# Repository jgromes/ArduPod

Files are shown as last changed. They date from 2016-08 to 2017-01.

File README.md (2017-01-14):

# ArduPod

<a href="http://www.youtube.com/watch?feature=player_embedded&v=DwULq69LcQs" target="_blank">ArduPod Remote Control</a>

## Open Source Arduino Hexapod
**Did you read the main ArduPod article at [DevicePlus](http://www.deviceplus.com/how-tos/arduino-guide/how-to-arduino-hexapod-part-1-mechanics-and-wiring/)? And the [second one](http://www.deviceplus.com/how-tos/arduino-guide/arduino-hexapod-part-2-programming/)? AND the [third one](http://www.deviceplus.com/how-tos/arduino-guide/arduino-hexapod-part-3-remote-control/)?**

If not, go read them, they're cool! If you did, and still didn't run away, good job! Here you will find all the files used in the article.

* **/arduino/**

   Contains all Arduino-related code; mainly examples and AP_Utils library.
   
   See [/arduino/AP_Utils/README.md](https://github.com/Gipsonek/ArduPod/blob/master/arduino/AP_Utils/README.md) for library details.

* **/model/**

   Files for 3D printing in the following formats: STL, SolidWorks parts, SketchUp
   
   See [/model/stl/printing_instructions.txt](https://github.com/Gipsonek/ArduPod/blob/master/model/stl/printing_instructions.txt) for details.

* **/processing/**

   Processing app source codes

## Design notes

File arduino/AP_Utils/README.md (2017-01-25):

# ArduPod Utilities Library

DISCLAIMER: This library is provided 'AS IS'. See ```license.txt``` for details.

IMPORTANT: Please note that this library requires [Adafruit PWM driver library](https://github.com/adafruit/Adafruit-PWM-Servo-Driver-Library) to be properly installed in your ```libraries``` folder. Adafruit PWM library is currently not provided with AP_Utils and has to be installed separately!

This library allows even less Arduino-experienced users to program their ArduPod. The main part of this library is lower-level servo and sensor control, plus a higher-level API in Arduino style that allows for easy ArduPod control. The following is a list of currently implemented features and their description, see ```./examples/``` for details on their usage.

* `AP_Utils(void)`

  Default constructor, used to create AP\_utils object, ie. `AP_Utils ardupod;`

* `begin(int *offsets)`

  This method performs initial setup, similarly to calling `Serial.begin(9600);` you have to call `ardupod.begin(offsets);` before calling any other methods. The `offsets` is an integer array with 16 members. This is to calibrate all the servos to the middle position. See `examples/calibration.ino` for details.

  **Note**: It is necessary to adjust few settings in `AP_Utils.h` according to the physical boundaries of the servos used. On lines 19 and 20, both variables have to be adjusted so that the servos won't get damaged. The easiest approach to this is to set the `SERVOMIN` value higher and `SERVOMAX` lower and uploading the `examples/servo_test.ino`. The servo will try to move back and forth from one end to the other. If the servo isn't reaching the physical limit, adjust the settings back towards their former value a bit, then upload again and oserve the differnce. Repeat this process until the servo is moving to both its limits while not stepping over them! Setting the `SERVOMAX` too high (or `SERVOMIN` too low) might destroy your servo!

  Also in `AP_Utils.h`, on line 12 ther is an option for debug mode. When uncommented, debug data will be sent to the serial port. It is highly recommended to not use this option unless absolutely necessary, as it will slow down everything else considerably.

* `moveServo(uint8_t servo, int deg. bool smooth = true, float speed = 2.5)`

  Move servo number `servo` (numbering consistent with Adafruit PWM Shield from 0 to 15) to position `deg` (where 0 and 180 degrees are the servos physical boundaries). If `smooth` is set to `true`, then the movement will be smooth. The `speed` arguement is optional and defines the speed at which the servo will move, with higher value meaning slower movement.  The value for this can vary for each servo type, most common values are from 2.0 to 5.0.

* `reset(int *offsets)`

  Reset all servos to their middle position with supplied offsets. See `examples/calibration.ino` for details.

* `traceLeg(uint8_t leg, float phi, float z, int resolution)`

  This method calculates a path for specified `leg` to follow, where `phi` and `z` are the leg ending positions and `resolution` is the path resolution. Note that this function itself won't move the leg, it will only return the path as an array of `pointLeg` structures.

* `setLegs(pointLeg *legs, uint8_t *numLegs, uint8_t total, bool smooth = true, float speed = 2.5)`

  Move the `legs` whose numbers are specified in array `numLegs` (the total number of moving legs has to be supplied by the `total` argument). This function will effectively move legs to the positions specified by `legs`, while driving all of them at once. See `examples/walk.ino` for details. 
  
  **Note**: It is NOT possible to achieve the same effect by using multiple calls to `moveServo`, as this function will only move one servo at a time!

* `stretch(void)`
  Raise and lower all the legs. This can be useful when one of the legs gets stuck.

* `step(int direction)`
  ArduPod will take a single step in the given direction. Supported directions are `FORWARD`, `BACKWARD`, `LEFT` and `RIGHT`. Note that `LEFT` and `RIGHT` will turn the robot one step (approx. 30 degrees).

* `walk(int direction)`
  Each time this function is called, Ardupod will walk one step in the given direction. Unlike the `step` function however, legs will not be reset to the default position, allowing for continous movement by calling this function again. Supported directions are `FORWARD`, `BACKWARD`, `LEFT` and `RIGHT`. Note that `LEFT` and `RIGHT` will turn the robot on the spot.

* `sr04(uint8_t trig, uint8_t echo, int unit)`

  Take a single measurement with HC-SR04 rangefinder. `trig` and `echo` are numbers of Arduino pins to which the SR04 TRIG and ECHO pins are connected. The result will be returned as a floating point number with unit specified by `unit`: currently supported constants are `MM` for millimters, `CM` for centimiters, and `M` for meters.

* `sr04_average(uint8_t trig, uint8_t echo, int unit, int samples, int time)`

  Take muber of measurements specified by `samples` over `time` milliseconds. The result will be an average of these measurements returned as floating point number with the specified unit.

* `sr04_median(uint8_t trig, uint8_t echo, int unit, int samples, int time)`

  Similar to the above, however, this method returns median of all the measurements. This function is recommended over `sr04_average` as it's result are much less prone to be affected by exceedingly wrong measurements.

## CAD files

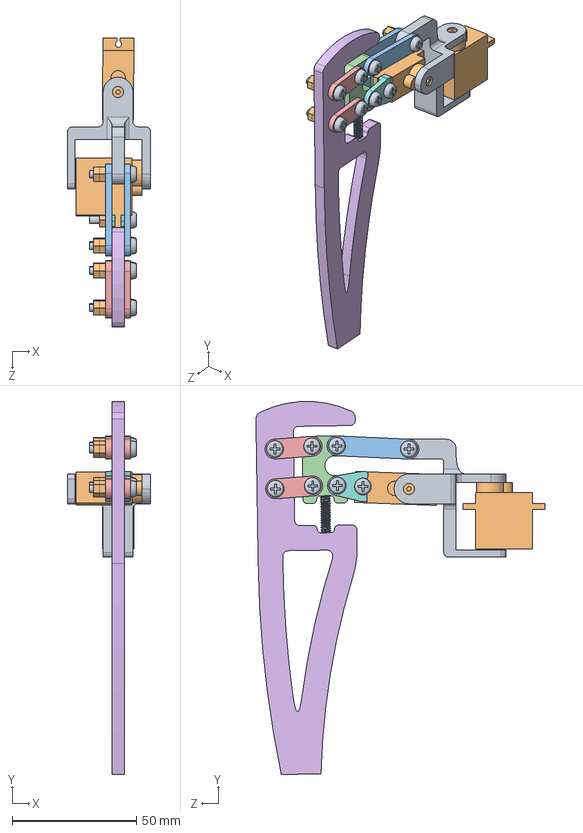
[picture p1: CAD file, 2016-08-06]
model/SolidWorks/leg.SLDASM
33.5 x 150.1 x 116.4 mm
leg2_v2
servo x 2
leg_bond2_f_v2 x 2
leg1_seg1_v2
leg_bond1_f_v2 x 4
leg1_v2
spring2
leg3_f_v2 x 2
bolt x 8
nut x 15

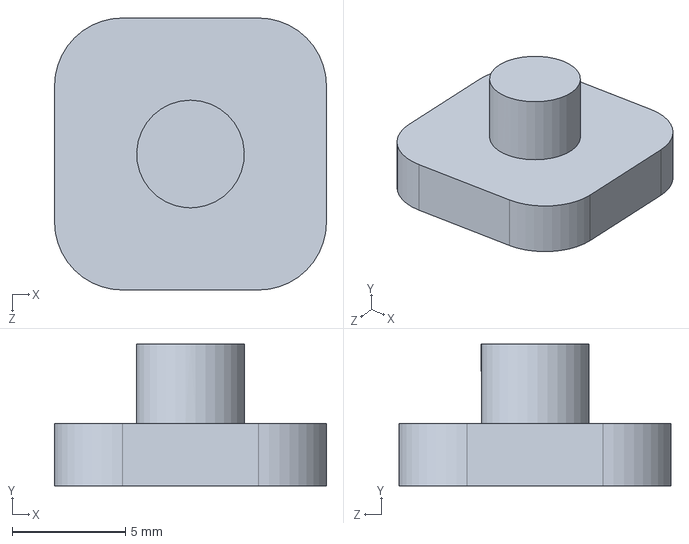
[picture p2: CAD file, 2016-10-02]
model/SolidWorks/leg2_seg1.SLDPRT
12.0 x 6.25 x 12.0 mm

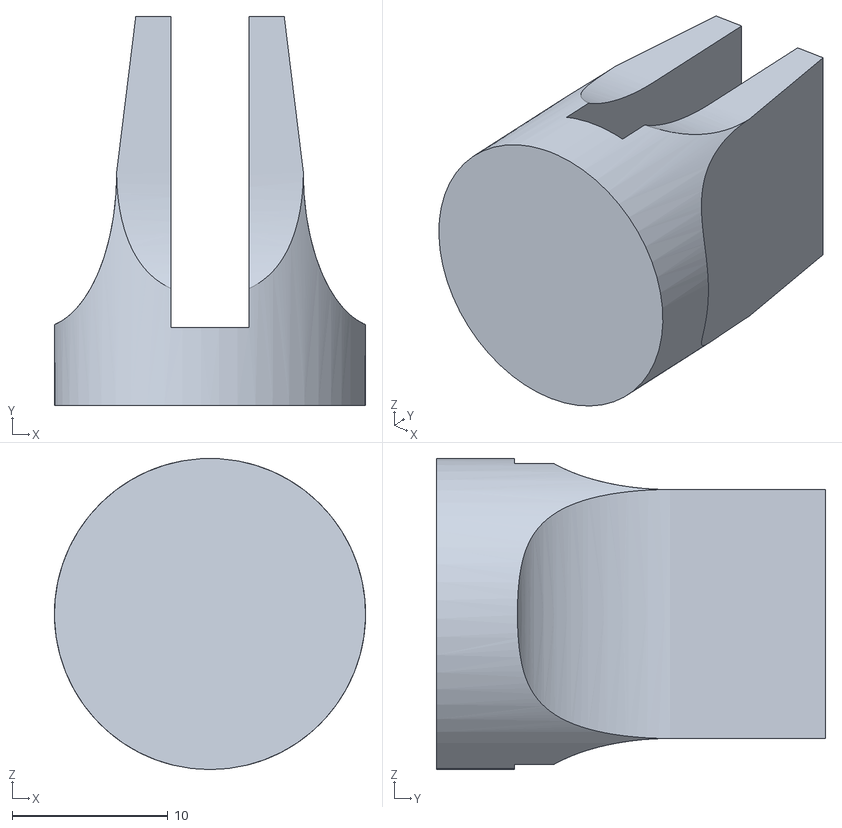
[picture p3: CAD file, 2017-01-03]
model/stl/leg4.STL
20.0 x 25.0 x 20.0

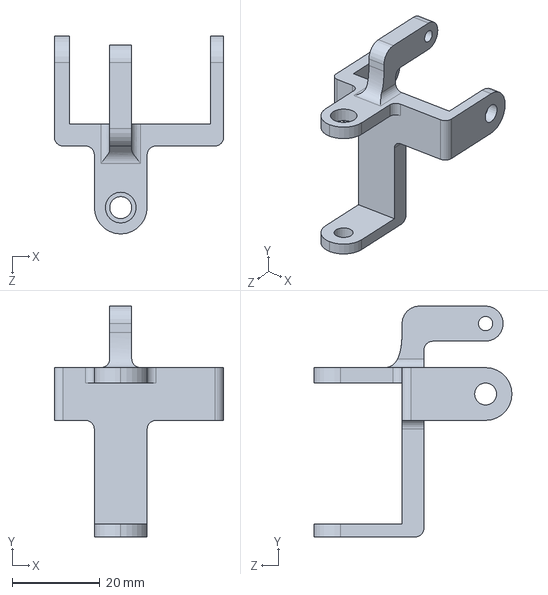
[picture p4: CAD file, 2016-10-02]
model/SolidWorks/leg2.SLDPRT
38.5 x 52.5 x 45.0 mm

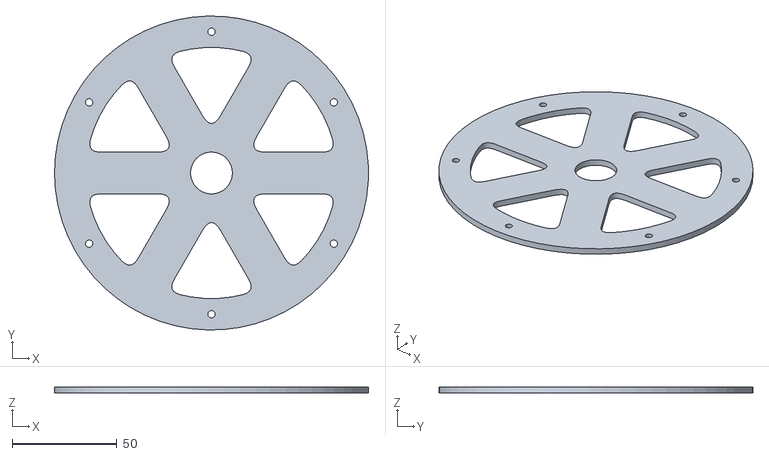
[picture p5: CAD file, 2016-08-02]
model/stl/body_bottom.STL
150.0 x 150.0 x 3.00

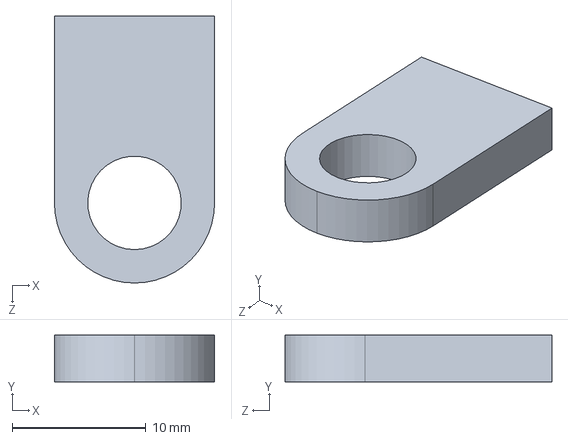
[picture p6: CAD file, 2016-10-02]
model/SolidWorks/leg2_segB.SLDPRT
12.0 x 3.50 x 20.0 mm

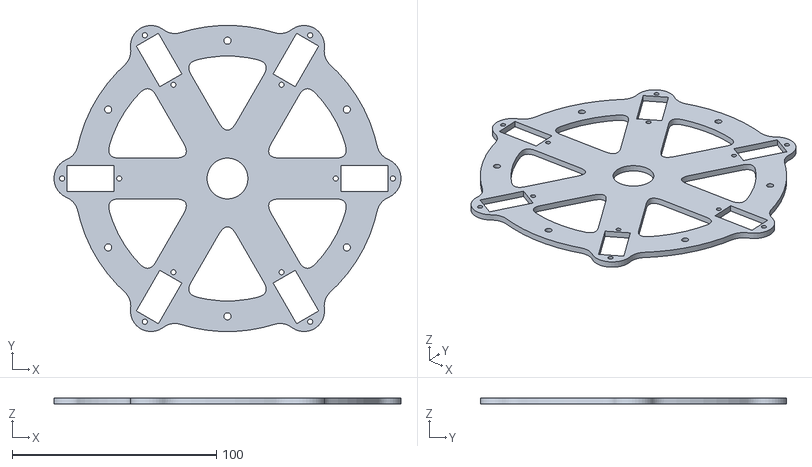
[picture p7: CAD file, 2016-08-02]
model/stl/body_top.STL
169.9 x 149.9 x 3.00

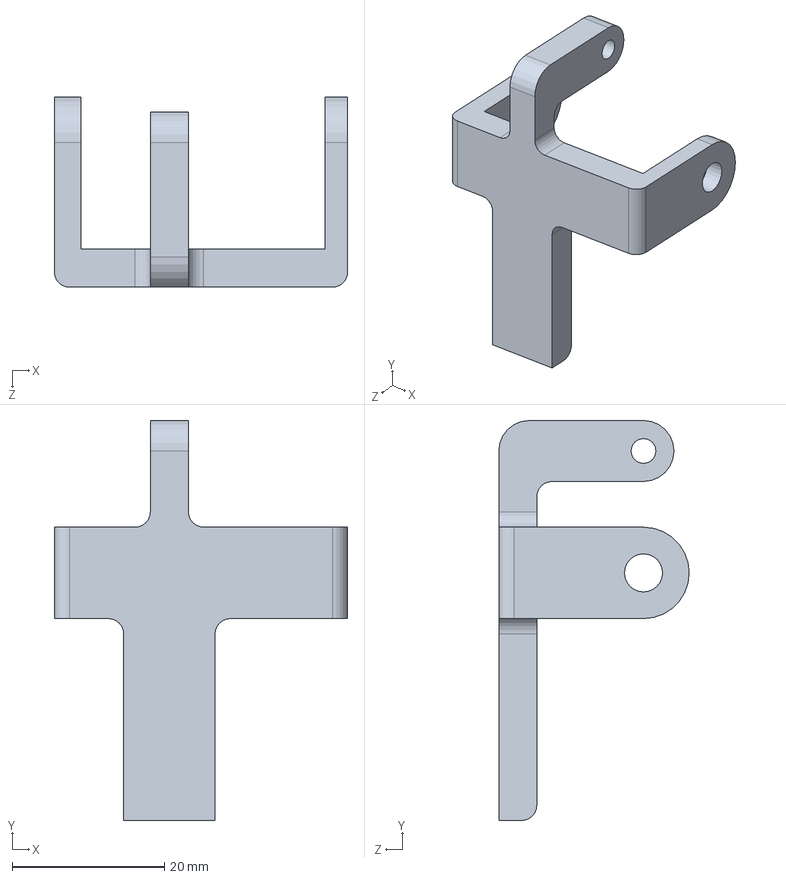
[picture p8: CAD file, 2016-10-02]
model/SolidWorks/leg2_segA.SLDPRT
38.5 x 52.5 x 25.0 mm

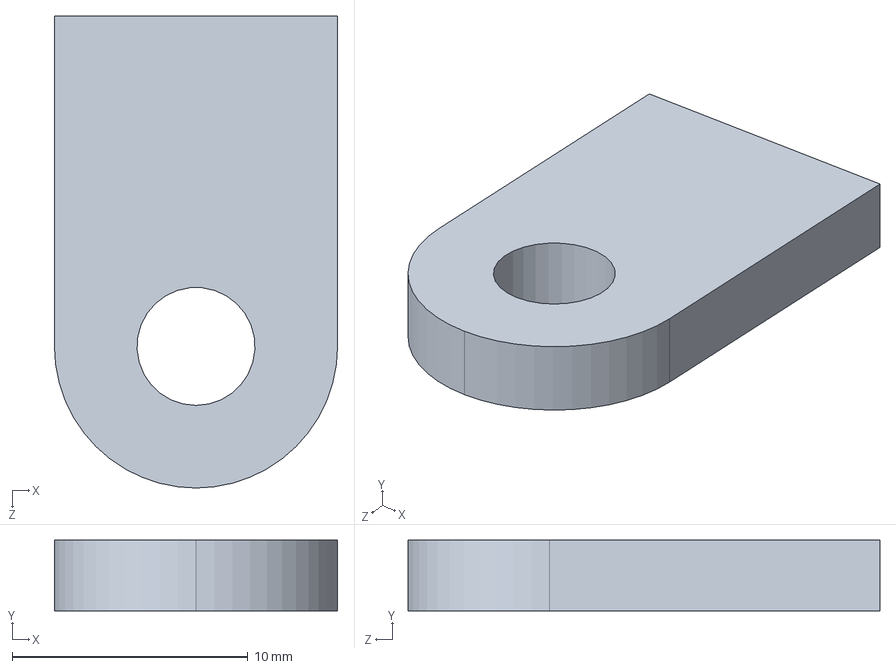
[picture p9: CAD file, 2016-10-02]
model/SolidWorks/leg2_segC.SLDPRT
12.0 x 3.00 x 20.0 mm

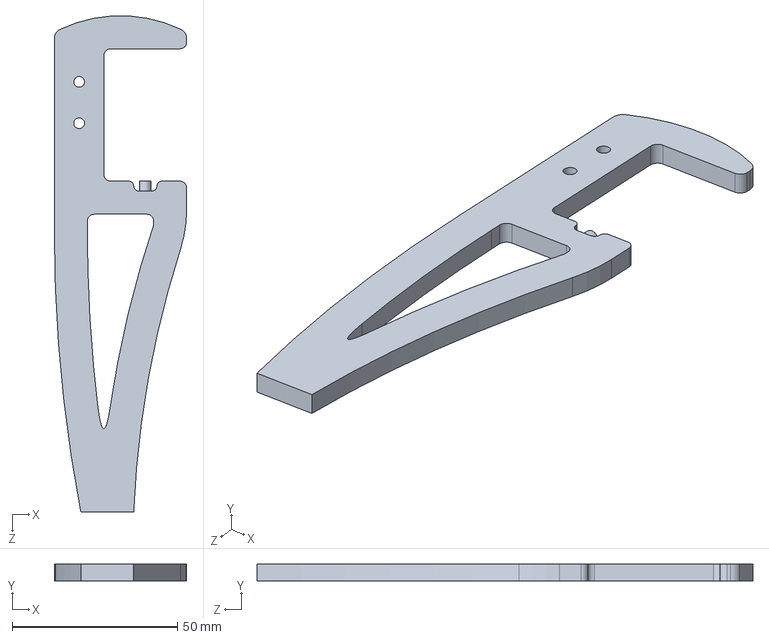
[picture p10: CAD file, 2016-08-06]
model/SolidWorks/leg1.SLDPRT
40.0 x 5.00 x 149.9 mm

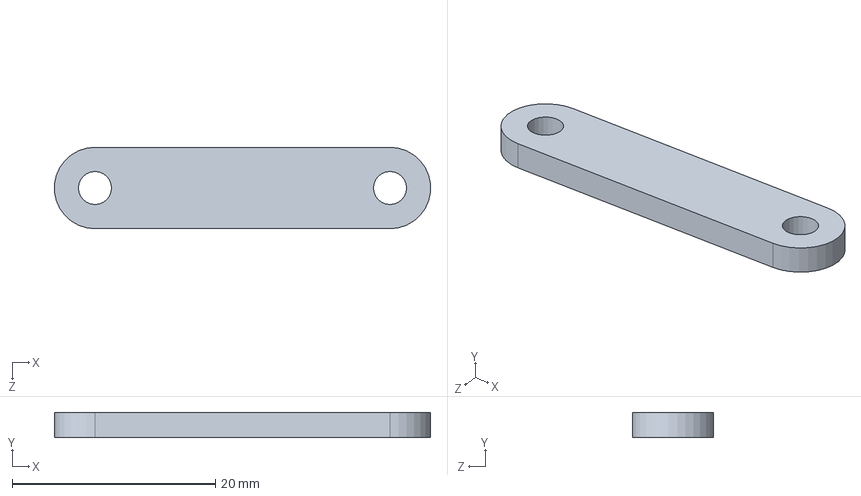
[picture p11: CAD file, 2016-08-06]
model/SolidWorks/leg_bond2_f.SLDPRT
37.0 x 2.50 x 8.00 mm

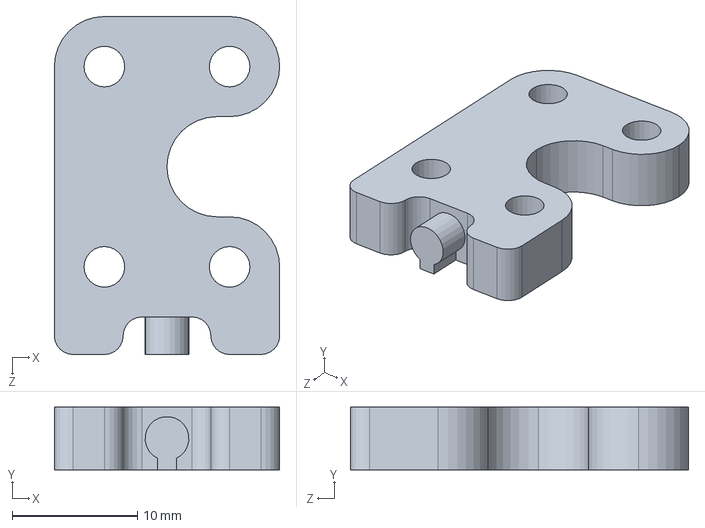
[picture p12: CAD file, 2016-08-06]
model/SolidWorks/leg1_seg1.SLDPRT
18.0 x 5.00 x 27.0 mm

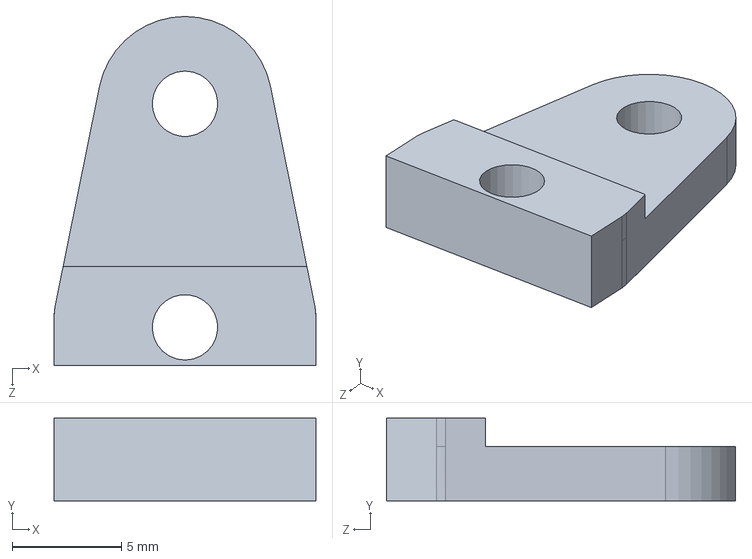
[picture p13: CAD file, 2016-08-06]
model/SolidWorks/leg3_f.SLDPRT
12.0 x 3.80 x 16.0 mm

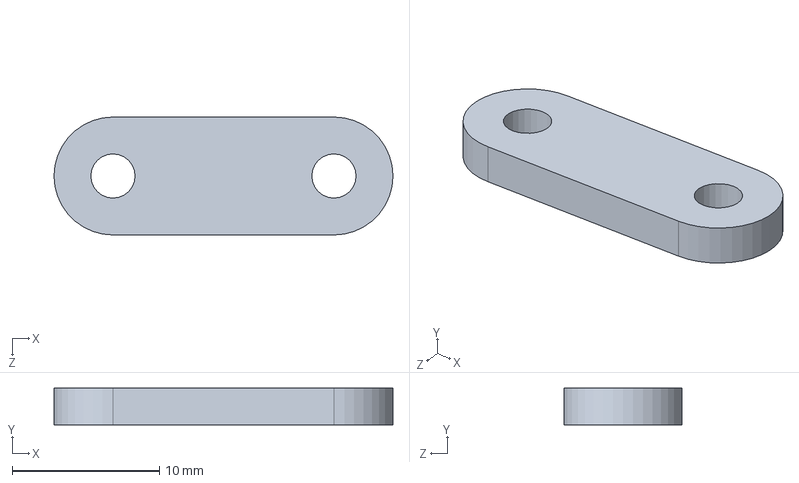
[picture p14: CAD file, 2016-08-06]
model/SolidWorks/leg_bond1_f.SLDPRT
23.0 x 2.50 x 8.00 mm

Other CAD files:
model/SketchUp/body_bottom.skp
model/SketchUp/body_top.skp
model/SketchUp/leg1.skp
model/SketchUp/leg1_seg1.skp
model/SketchUp/leg2.skp
model/SketchUp/leg2_seg1.skp
model/SketchUp/leg2_segA.skp
model/SketchUp/leg2_segB.skp
model/SketchUp/leg2_segC.skp
model/SketchUp/leg_bond1.skp
model/SketchUp/leg_bond2.skp
model/stl/leg1.STL
model/stl/leg1_seg1.STL
model/stl/leg2.STL
model/stl/leg2_seg1.STL
model/stl/leg2_segA.STL
model/stl/leg2_segB.STL
model/stl/leg2_segC.STL
model/stl/leg3_f.STL
model/stl/leg_bond1_f.STL
model/stl/leg_bond2_f.STL

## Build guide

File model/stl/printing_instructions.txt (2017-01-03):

Part name	# of prints needed
--------------------------------
body_bottom	1x
body_top	1x
leg1		6x
leg1_seg1	6x
leg2_seg1	12x
leg2_segA	6x
leg2_segB	6x
leg2_segC	6x
leg3_f		12x
leg4            6x
leg_bond1_f	24x
leg_bond2_f	12x

Alternatively, instead of printing leg_segA,B and C, you can just print leg2.
However, that will require precisely calibrated printer. See the SolidWorks or SketchUp file for details.

Before printing, make sure that all the holes are the correct size. If you're using M3 bolts for the moving parts,
you will need the holes to have at least 3.25mm in diameter. The two bigger holes in leg2(_segA) are for the servo's gear axis.
Make sure their diameter is the same as the one of the gear axis on the servos you are using. 
In body_bottom, you will find rectangle-shaped holes for mounting the horizontal servos. 
Make sure they are big enough for the servos you will be using. To mount these servos, you will probably need to take them apart,
slide them in and reassemble them.

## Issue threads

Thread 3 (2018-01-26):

I need to use this application from android phone

Cretu93, 2018-01-26:
Hello,

How can I use processing app on android phone.
I don't see where you use bluetooth comnunication with another device that can send commands.
I need to use your buttons from app to send comand through bluetooth not serial.
Could you please help me?

jgromes, 2018-01-26:
Unfortunately, the processing app was written to be only used on PC. Even though Processing IDE has an "Android" mode, I don't have any experience with it. Besides, the way Bluetooth communication is handled on Android devices is fundamentally different from the approach I used: in the app, the commands are sent to Serial port which has USB Bluetooth adapter connected to it. Also, the app requires some Processing libraries, and I'm not sure if they would work on Android.

I doubt you will be able to use this app from Android phone as it is written right now - that would probably require substantial modifications. Instead, I would recommend using Android studio to write a new app. As a sort of starting point, you can take a look at my [ArduRover](https://github.com/jgromes/ArduRover) project. In the `android` directory, you will find an Android app that can send data either through Bluetooth, or through USB port.

Closed 2018-10-03.

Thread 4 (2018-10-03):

Any way I can use an Uno by doing the possessing elsewhere?

Chroniton4X, 2018-10-03:
Hi, I have designed and 3d printed my own 2 DOF hexapod based around the Arduino Uno (particularly its dimensions) prior to finding out its lack of processing power for IK. Switching to the mega would mean I need to redesign and print the whole chassis again. Is there any way I could do all the processing on an external laptop or Arduino Mega and just send the servo positions to the Uno onboard the robot over Bluetooth?

jgromes, 2018-10-04:
The simplest one is probably Processing (https://processing.org/), there are loads of tutorials on connecting it to Arduino. Just keep in mind that even though it looks similar to Arduino IDE, the language is Java, not C/C++.

If you're looking something more professional, I suggest Visual Studio and writing the PC app in C#. Working with GUI elements is much easier than in Processing.

Chroniton4X, 2018-10-09:
I just got a cheap Arduino Mega clone and I'm going to design and print a new chassis for it. I want to add some more sensors to the robot later and maybe control it with a smartphone so I will need more processing power anyway. Also, it should be easier since I don't have to convert to Java.

     I can do 3d modeling and electronics but I'm new to programming in C++. This project is mostly for teaching my self C++ and the Arduino so I make design, wire, and program things.

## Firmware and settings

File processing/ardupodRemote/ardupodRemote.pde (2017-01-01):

import processing.serial.*;
import controlP5.*;

ControlP5 cp5;

Serial port;
String[] comList;
int portNum;
boolean selected = false, connected = false, firstScan = false;

int[] scanResults = new int[180];
boolean startScan = false;
int posScan = 0;
int posLine = 90;
int lastAngleSliderValue = 90;

void setup() {
  size(960, 480);
  background(#888888);
  frameRate(120);
  comList = Serial.list();
  guiSetup();
}

public void serialInput(String s) {
  output(11, 9, s);
  if(s.equals("version") || s.equals("v")) {
    output(11, 8, version);
  }
}

public void serialOutput(String s) {
  //tab size fix
  s = s.replaceAll("\t", "        ");
}

public void angleSlider(int angle) {
  posLine = angle;
}

public void portsList(int n) {
  selected = true;
  portNum = n;
}

void mouseReleased() {
  if(angleSlider.isMouseOver() && (lastAngleSliderValue != (int)angleSlider.getValue()) && !(startScan)) {
    lastAngleSliderValue = (int)angleSlider.getValue();
    output(11, 10, "Turning sensor: " + (int)angleSlider.getValue() + "°");
    if(connected) {
      port.write("t" + str((int)angleSlider.getValue()));
    }
  }
}

long lastKey;
void keyPressed() {
  switch(key) {
    case 'w':
      if(!inputField.isFocus()) {
        moveW.setColorBackground(color(0x00, 0xAA, 0xFF));
        moveW.lock();
        if(millis()-lastKey >= 1000) {
          lastKey = millis();
          output(11, 10, "Walk forward");
          if(connected){port.write("w");}
        }
      }
      break;
    case 'a':
      if(!inputField.isFocus()) {
        moveA.setColorBackground(color(0x00, 0xAA, 0xFF));
        moveA.lock();
        if(millis()-lastKey >= 1000) {
          lastKey = millis();
          moveA.setOn();
          output(11, 10, "Turn left");
          if(connected){port.write("a");}
        }
      }
      break;
    case 's':
      if(!inputField.isFocus()) {
        moveS.setColorBackground(color(0x00, 0xAA, 0xFF));
        moveS.lock();
        if(millis()-lastKey >= 1000) {
          lastKey = millis();
          moveS.setOn();
          output(11, 10, "Walk backward");
          if(connected){port.write("s");}
        }
      }
      break;
    case 'd':
      if(!inputField.isFocus()) {
        moveD.setColorBackground(color(0x00, 0xAA, 0xFF));
        moveD.lock();
        if(millis()-lastKey >= 1000) {
          lastKey = millis();
          moveD.setOn();
          output(11, 10, "Turn right");
          if(connected){port.write("d");}
        }
      }
      break;
  }
}

void keyReleased() {
  switch(key) {
    case 'w':
      moveW.setColorBackground(color(0x00, 0x2D, 0x5A));
      moveW.unlock();
      break;
    case 'a':
      moveA.setColorBackground(color(0x00, 0x2D, 0x5A));
      moveA.unlock();
      break;
    case 's':
      moveS.setColorBackground(color(0x00, 0x2D, 0x5A));
      moveS.unlock();
      break;
    case 'd':
      moveD.setColorBackground(color(0x00, 0x2D, 0x5A));
      moveD.unlock();
      break;
  }
}

long lastMouse;
public void controlEvent(ControlEvent theEvent) {
  switch(theEvent.getController().getName()) {
    case "scanButton":
      scanButton.setLabel("scanning...");
      if(connected){port.write("n");}
      posScan = 0;
      posLine = 0;
      break;
    case "measureButton":
      if(connected){port.write("m");}
      break;
    case "connectButton":
      if(selected) {
        try {
          if(!connected) {
            port = new Serial(this, Serial.list()[portNum], 9600);
            connected = true;
            output(11, 8, "Connected to " + Serial.list()[portNum]);
          }
        } catch(Exception e) {
          output(11, 6, "Unable to connect to " + Serial.list()[portNum]);
          output(11, 6, e.toString());
          connected = false;
        }
      } else {
        output(11, 6, "Select appropriate COM port");
      }
      break;
    case "disconnectButton":
      if(connected) {
        output(11, 8, "Disconnected from " + Serial.list()[portNum]);
        port.stop();
        connected = false;
      }
      break;
    case "W":
      if(millis()-lastMouse >= 1000) {
        lastMouse = millis();
        output(11, 10, "Step forward");
        if(connected){port.write("ws");}
      }
      break;
    case "A":
      if(millis()-lastMouse >= 1000) {
        lastMouse = millis();
        output(11, 10, "Step left");
        if(connected){port.write("as");}
      }
      break;
    case "S":
      if(millis()-lastMouse >= 1000) {
        lastMouse = millis();
        output(11, 10, "Step backward");
        if(connected){port.write("ss");}
      }
      break;
    case "D":
      if(millis()-lastMouse >= 1000) {
        lastMouse = millis();
        output(11, 10, "Step right");
        if(connected){port.write("ds");}
      }
      break;
  }
}

void receiveData() {
  String input = port.readStringUntil('\n');
  String payload;
  int code1, code2;
  if (input != null && input.charAt(0) != 0) {
    code1 = (int)input.charAt(0)-48;
    code2 = (int)input.charAt(1)-48;
    payload = trim(input.substring(2));
    if((code1 == 4) && (code2 == 0)) {
      if(payload.equals("s")) {
        startScan = true;
        scanButton.lock();
        angleSlider.lock();
      } else {
        int distance = Integer.parseInt(trim(payload));
        if((distance < 200) && (distance > 0)) {
          scanResults[posLine] = distance;
        } else {
          scanResults[posLine] = 200;
        }
        drawScan(posLine);
        angleSlider.setValueLabel(str(posLine));
        posLine++;
        if(posLine == 180) {
          firstScan = true;
          startScan = false;
          scanButton.unlock();
          scanButton.setLabel("scan");
          angleSlider.unlock();
        }
      }
    } else if((code1 == 4) && (code2 == 1)) {
      distanceArea.setText(payload + " cm");
    } else {
      output(code1, code2, payload);
    }
  }
}

void draw() {
  background(#666666);
  CP5AddOns();
  drawRefreshLine(posLine);
  
  if(connected) {
    receiveData();
  }
}

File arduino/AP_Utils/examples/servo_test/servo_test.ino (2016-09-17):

/*
 * Servo test sketch
 * 
 * Used to calibrate the maximum and minimum boundaries for the servos.
 * It is absolutely necessary to run this example and calibrate the servos you will be using.
 * 
 * Calibration guide:
 * After uploading this example, the first servo (number 0) will sweep from the minimum to the maximum position.
 * You have to check whether it is reaching its physical limit.
 * The easiest way to do that is to disconnect power to the servo shield when the servo is in one of the limit positions.
 * With disconnected power, try to move the servo further in the direction it was moving before.
 * If it can still be moved, try to tweak the 'SERVOMIN' (or 'SERVOMAX') a little bit (about 10 at a time).
 * Do NOT try to move the servo beyond its physical limit, this might destroy your servo!
 * 
 * Brought into existence and debugged out of it by Gipsonek, 2016
 */

#include <Adafruit_PWMServoDriver.h>

//default SERVOMIN and SERVOMAX values
//be extremely careful when changing these, only in small incremets (about 10) at a time
//too big change (100 and more) can cause your servos gears to break!
#define SERVOMIN 150
#define SERVOMAX 530

//create Adafruit PWM Servo Driver object to directly control the PWM outputs
Adafruit_PWMServoDriver pwm = Adafruit_PWMServoDriver();

void setup() {
  Serial.begin(9600);
  pwm.begin();
  pwm.setPWMFreq(60);
}

void loop() {
  //move from max position to min
  for(int pulse=SERVOMAX; pulse>=SERVOMIN; pulse--) {   
    pwm.setPWM(15, 0, pulse);
    Serial.println(pulse);
    delay(10);
  }
  delay(3000);

  //move from min position to max
  for(int pulse=SERVOMIN; pulse<=SERVOMAX; pulse++) {   
    pwm.setPWM(15, 0, pulse);
    Serial.println(pulse);
    delay(10);
  }
  delay(3000);
}

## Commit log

2016-08-02 Initial commit, added STL models and AP_Utils library
    [body_bottom.STL, body_top.STL, leg1.STL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]
2016-08-06 Add SolidWorks models
    [leg.SLDASM, leg1.SLDPRT, leg1_seg1.SLDPRT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]
2016-08-13 Add SketchUp files
    [body_bottom.skp, body_top.skp, leg1.skp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]
2016-08-16 Fixed servo holder
    [leg2.skp, leg2_segA.skp, leg2_segB.skp]
2016-08-27 Added servo smoothing
2016-08-29 Fixed servo smoothing
2016-09-02 Servo smoothing fix
2016-09-02 Fixed servo holder for MG servos
    [leg2.SLDPRT, leg2_segB.SLDPRT]
2016-09-14 Added calibration and servo_test examples
2016-09-17 Servo_test update
2016-10-02 Servo holder update
    [leg2.STL, leg2_seg1.STL, leg2_segA.STL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]
